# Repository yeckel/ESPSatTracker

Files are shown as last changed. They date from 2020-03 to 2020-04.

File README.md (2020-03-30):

# ESPSatTracker (work still in progress, ideas wellcommend)

This project is intended for tracking HAM radio satellites using stock available cheep components and 3D printer. 
* Antena is 5+8 elem Yagi from [dk7zb](https://www.qsl.net/dk7zb/Duoband/5+8_2m-70cm.htm)
* Rotator was heavily inspired from [tysonpower.de](https://tysonpower.de/blog/diy-az-el-antenna-rotator-for-under-150)

## Features
It shall be remotely operated (Bluetooth), it shall bear heavier antennas (preparing for moonscating), it shall be portable, it shall bring fun.

## Parts used
* 2000 x 15 x 15 allu rectangle tube for antenna beam
* two 2000 x 20 x 20 allu rectangle tube for rotator frame and azimuth axe
* ?x 8mm allu tubes for yagi elements
* 1x 12mm allu tube for yagi radiator
* plenty of M4 screws with nuts and waschers
* 4mm plywood for rotator sides
* 2x TB6600 stepper drivers
* 2x NEMA24 stepper motors
* 2 endstops from eBay (optional and not really used)
* Wemos Lolin32 as rotator controller (other ESP32 development board should do too)
* PLA filanment (ABS was bending too much for big parts)

## Software used
* OpenSCAD & Slic3r & RepetierHost for 3d modelling and printing
* [platformio](https://platformio.org) for SW build
* gpredict for satellite tracking
* STL and scad projects and fotos are at [thingiverse](https://www.thingiverse.com/thing:4246844)

## Build
### Dependencies
Install platformio and libraries Streaming and ESP8266_SSD1306
```
platformio lib --global install Streaming
platformio lib --global install ESP8266_SSD1306
```
### Build and upload:
Run in the RotatorController directory
```
platformio run -t upload
```

### Start
1. Without power, orient the rotator to the north and level antena horizontally.
1. Power up motors and ESP32 controller
1. In your bluetooth search for a device named ESP32 Rotator and add that device.
1. In the terminal connect to it `sudo rfcomm connect 1 <device mac address>`
1. In another terminal window start a rotator control daemon `rotctld -r /dev/rfcomm1 -s 115200 -m 603` The 603 is a rotator model 603, 'GS-232B'
1. Then in gpredict add a new rotator. Choose some name, host is `localhost`, port: `4533`, Az type: `0 - 180 - 360`, Max Az:`360`, Max El: `180`

## Notes
The rotator can commands like speed and park to zero. However the rotctld nor it's stand-allone application are using them. Just stop, move to azimuth and elevation, asking for current azimuth and elevation is actually used by the daemon.

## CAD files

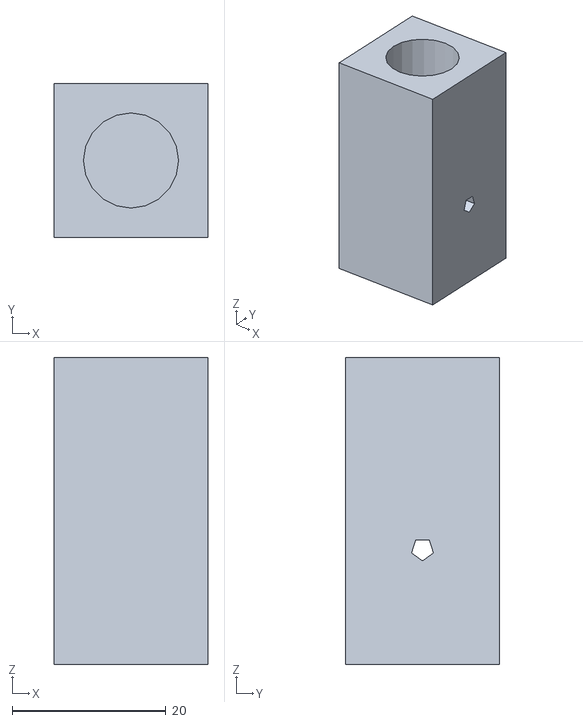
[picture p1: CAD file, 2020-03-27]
3dPrintedParts/stls/RadiatorDrillTool.stl
20.0 x 20.0 x 40.0

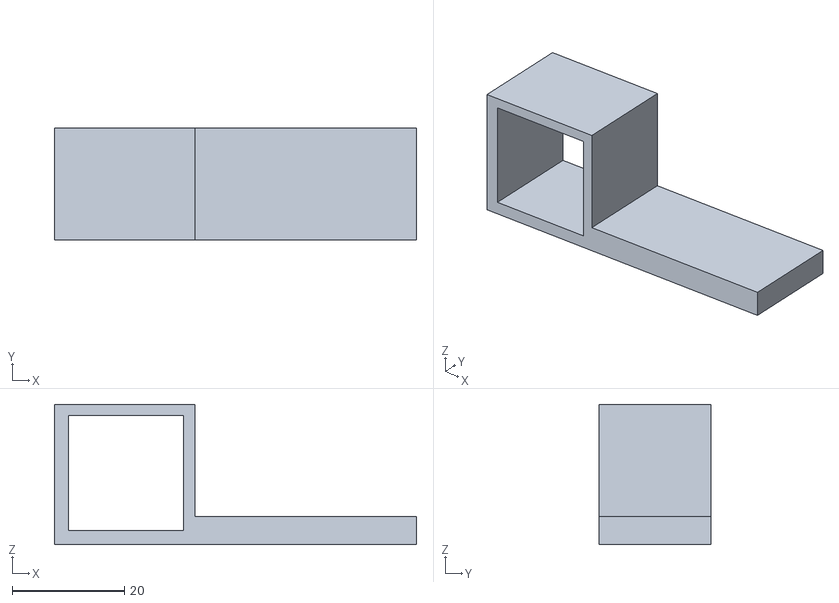
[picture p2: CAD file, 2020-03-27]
3dPrintedParts/stls/endstopEle.stl
64.5 x 20.0 x 25.0

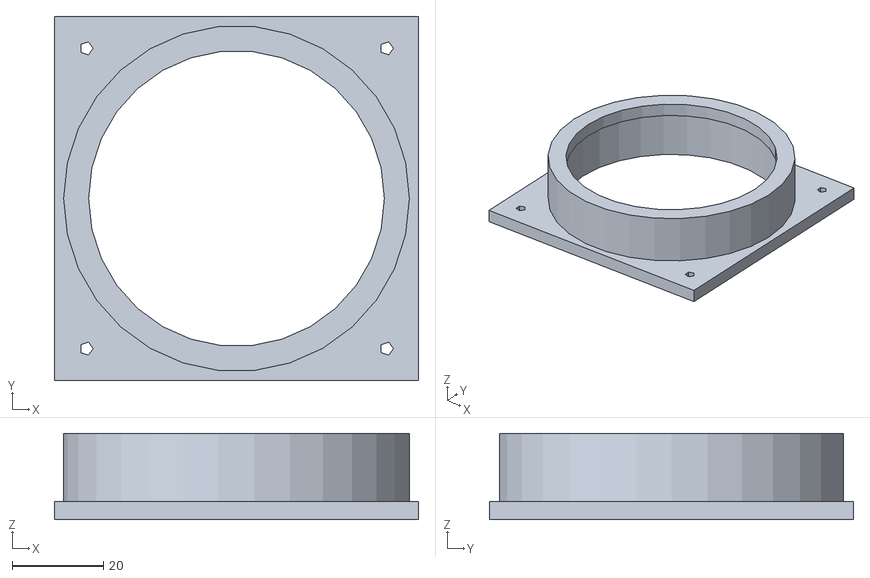
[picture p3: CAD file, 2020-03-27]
3dPrintedParts/stls/bearingHolder.stl
80.0 x 80.0 x 19.0

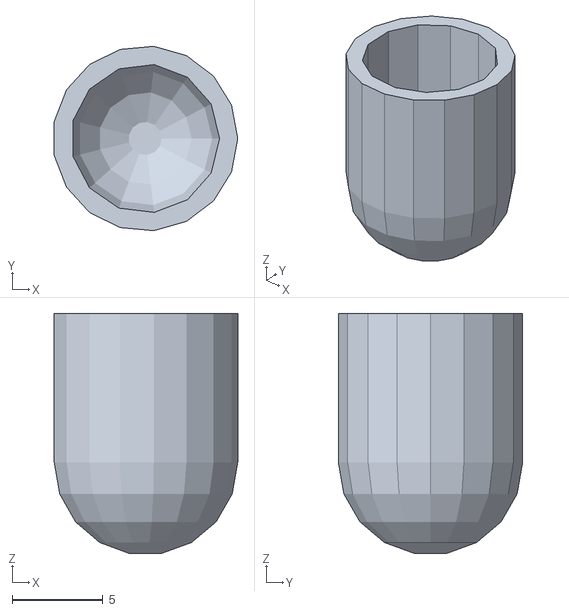
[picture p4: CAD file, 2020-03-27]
3dPrintedParts/stls/WireCap.stl
10.1 x 10.2 x 13.2

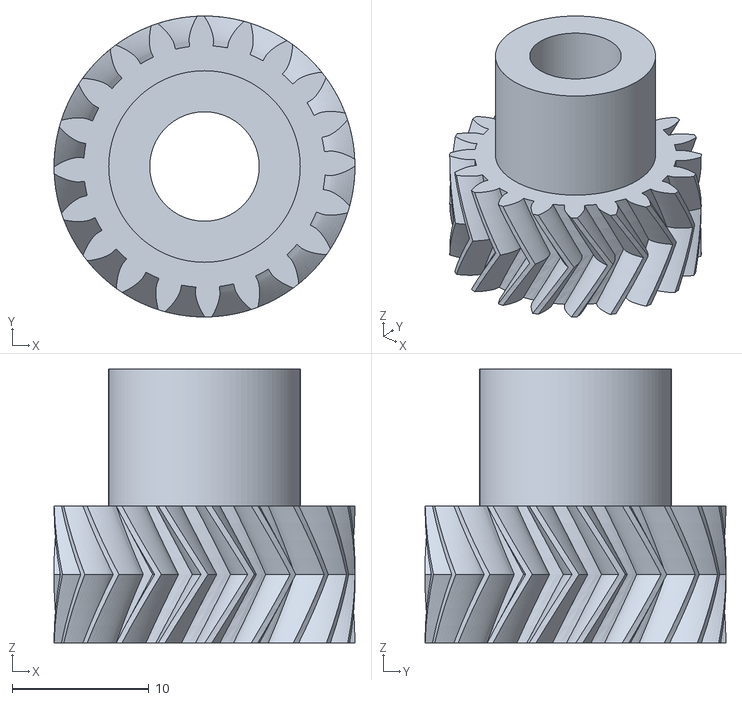
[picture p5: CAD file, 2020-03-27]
3dPrintedParts/stls/KoleckoKMotoru.stl
22.0 x 22.0 x 20.0

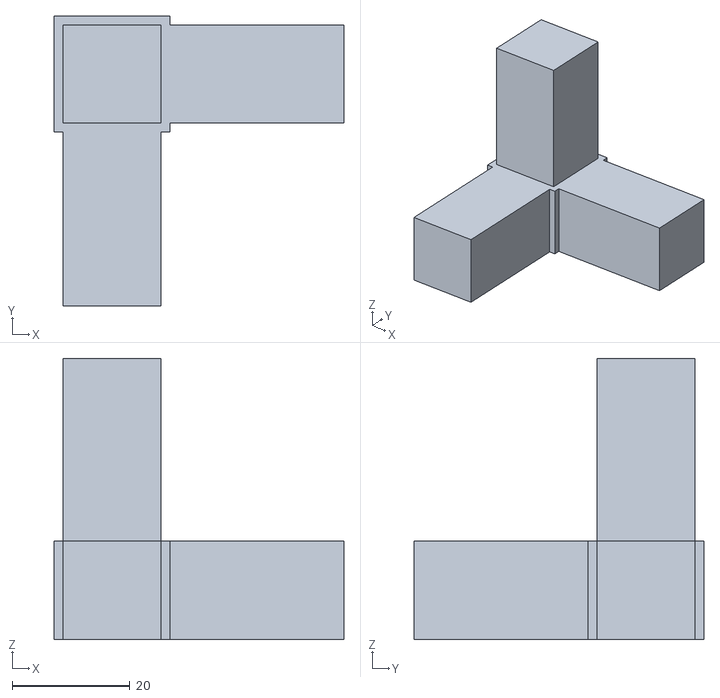
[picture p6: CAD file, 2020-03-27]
3dPrintedParts/stls/BoxCorner.stl
49.4 x 49.4 x 47.9

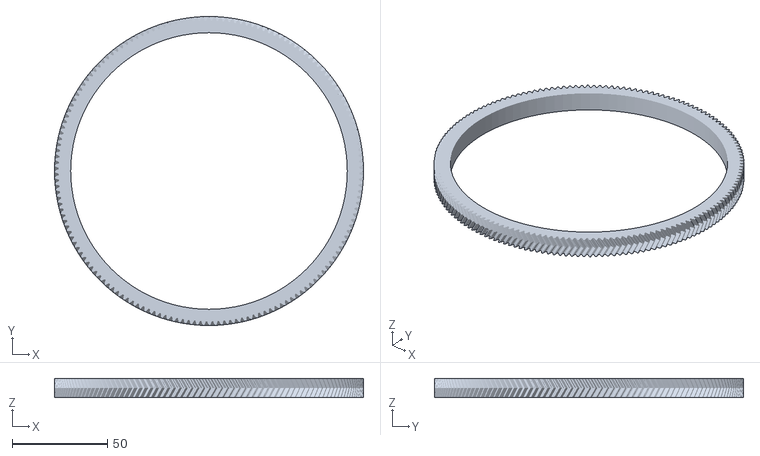
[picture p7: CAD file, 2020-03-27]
3dPrintedParts/stls/PrevodovkaRotator.stl
162.0 x 162.0 x 10.0

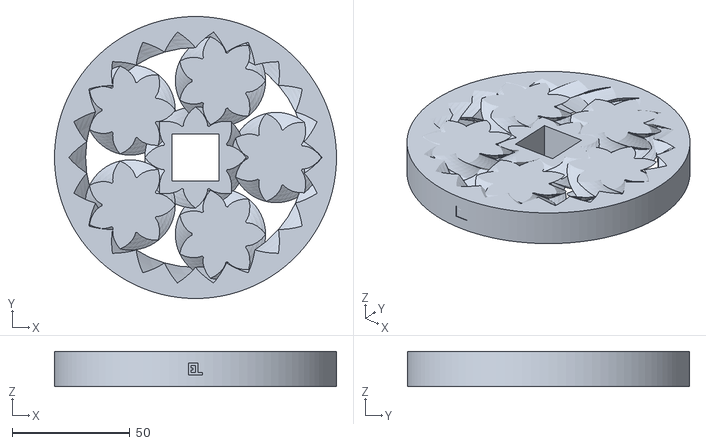
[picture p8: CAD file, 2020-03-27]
3dPrintedParts/stls/bearing.stl
120.0 x 120.0 x 15.0

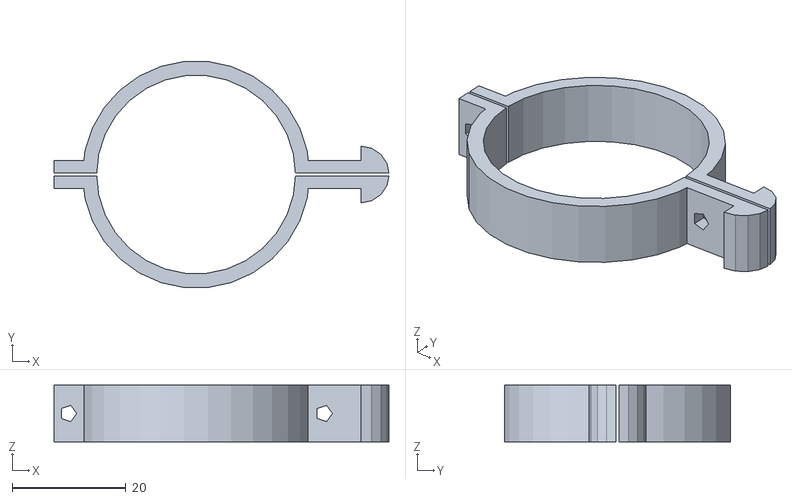
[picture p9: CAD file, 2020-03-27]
3dPrintedParts/stls/endstopAzi.stl
59.0 x 39.8 x 10.0

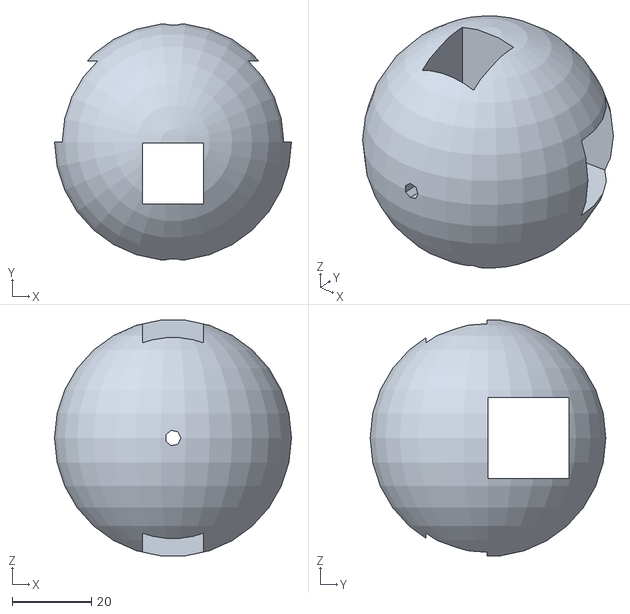
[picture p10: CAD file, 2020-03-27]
3dPrintedParts/stls/mast2yagi.stl
60.0 x 59.7 x 59.7

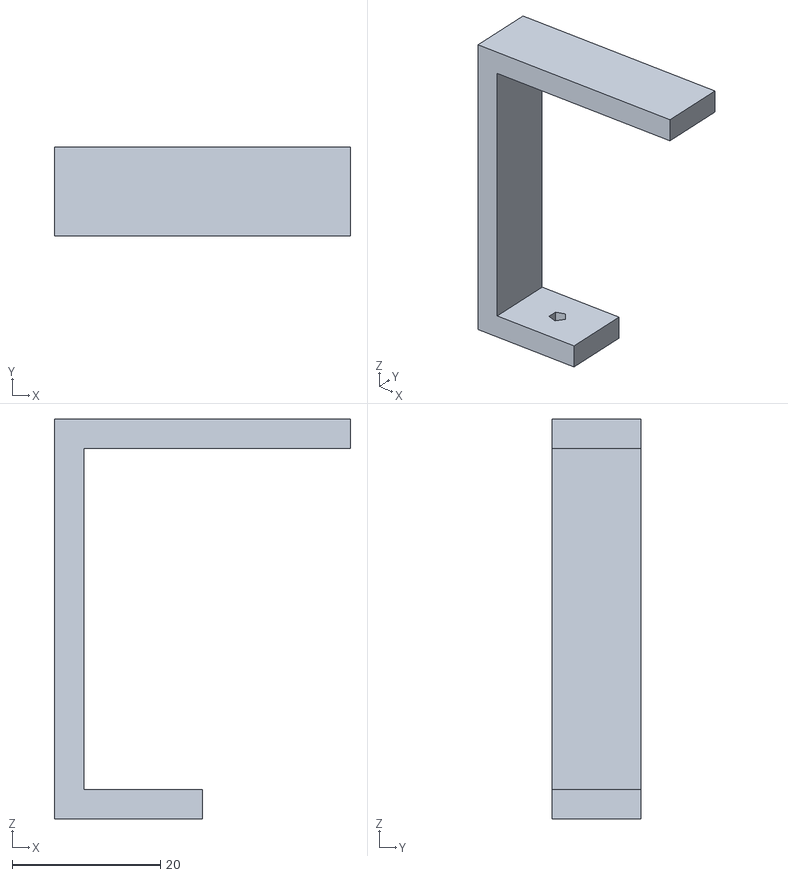
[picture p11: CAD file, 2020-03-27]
3dPrintedParts/stls/endstopHolder.stl
40.0 x 12.0 x 54.0

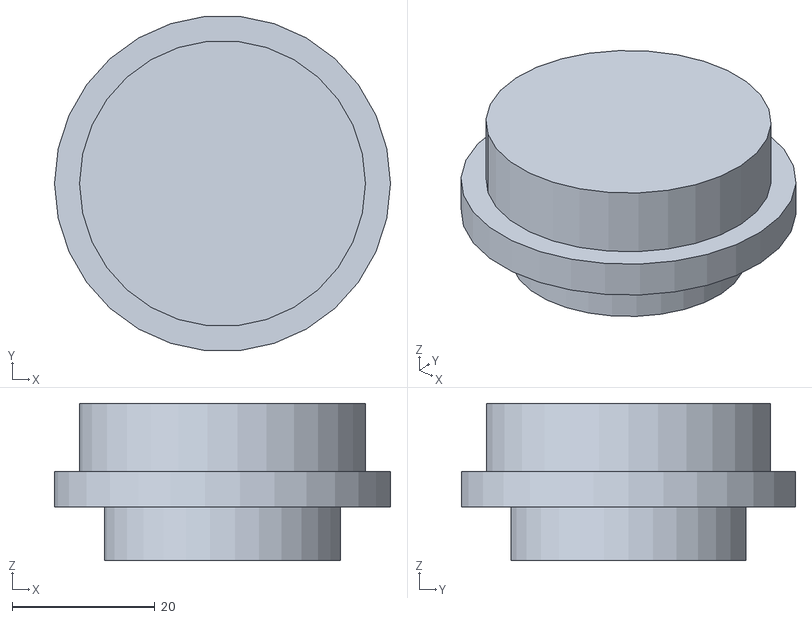
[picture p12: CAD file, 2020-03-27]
3dPrintedParts/stls/tripodCap.stl
47.0 x 46.7 x 22.0

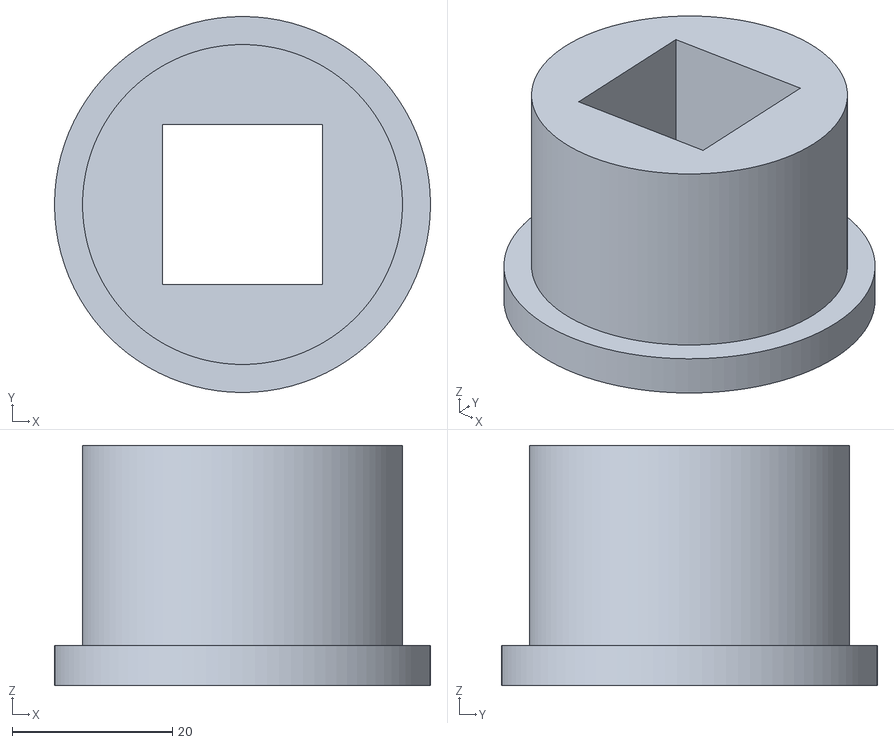
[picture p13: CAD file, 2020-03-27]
3dPrintedParts/stls/elevationHolder.stl
47.0 x 47.0 x 30.0

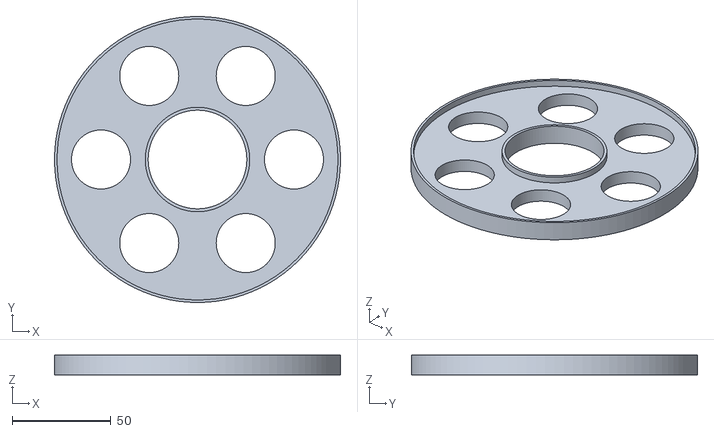
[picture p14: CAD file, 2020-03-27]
3dPrintedParts/stls/gearCenter.stl
145.0 x 145.0 x 10.0

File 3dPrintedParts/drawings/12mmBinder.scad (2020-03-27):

cylinder(h=50,d=10,center=true);
cylinder(h=2,d=12,center=true);

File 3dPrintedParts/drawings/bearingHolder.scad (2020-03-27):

difference(){
union(){
cylinder(d=76,h=19);//obal loziska stena 4mm
translate([0,0,2]) cube([80,80,4],center=true); //podstavec
}
cylinder(d=69,h=15); //lozisko
cylinder(d=65,h=30); //vnitrek loziska

translate([33,33,0]) cylinder(d=3,h=20);
translate([-33,-33,0]) cylinder(d=3,h=20);
translate([33,-33,0]) cylinder(d=3,h=20);
translate([-33,33,0]) cylinder(d=3,h=20);
}

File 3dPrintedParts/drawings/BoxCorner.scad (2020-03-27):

profil=20/1.013;
stena=3*1.4;

vnitek=profil-stena;

rotate([0,0,0]) translate([0,0,profil])cube([vnitek,vnitek,2*profil],center = true);
rotate([0,90,0]) translate([0,0,profil])cube([vnitek,vnitek,2*profil],center = true);
rotate([90,0,0]) translate([0,0,profil])cube([vnitek,vnitek,2*profil],center = true);
cube([profil,profil,profil-stena], center = true);

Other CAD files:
3dPrintedParts/stls/OuterGearRing.stl
3dPrintedParts/stls/yagi_director.stl
3dPrintedParts/stls/azimuthCoreWheel.stl
3dPrintedParts/stls/elevationCoreWheel.stl
3dPrintedParts/drawings/endstopAzi.scad
3dPrintedParts/drawings/RadiatorDrillTool.scad
3dPrintedParts/drawings/Rotator.scad
3dPrintedParts/drawings/Spojka90Stupnu.scad
3dPrintedParts/drawings/WireCap.scad
3dPrintedParts/drawings/endstopEle.scad
3dPrintedParts/drawings/endstopHolder.scad
3dPrintedParts/drawings/mast2yagi.scad
3dPrintedParts/drawings/tripodCap.scad
3dPrintedParts/drawings/yagi_director.scad
3dPrintedParts/drawings/yagi_radiator.scad

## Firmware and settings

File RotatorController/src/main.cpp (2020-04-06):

#include <Arduino.h>
#include <SSD1306Wire.h>
#include "BluetoothSerial.h"
#include <Streaming.h>

// DIY Sat Tracker Software by Tysonpower.de
// NOTE: The code works but it is NOT optimal nor bug free

// Implementation of the Yaesu GS232B Protocol
// B              - Report elevation                                EL=eee
// C              - Report azimuth                                  AZ=aaa
// C2             - Report azimuth and elevation                    AZ=888 EL=eee
// S              - Stop all rotation
// A              - Stop azimuth rotation
// E              - Stop elevation rotation
// L              - Rotate azimuth left (CCW)
// R              - Rotate azimuth right (CW)
// D              - Rotate elevation down
// U              - Rotate elevation up
// Mxxx           - Move to azimuth
// Wxxx yyy       - Move to azimuth xxxx and elevation yyy
// X1             - Change to azimuth rotation speed setting 1
// X2             - Change to azimuth rotation speed setting 2
// X3             - Change to azimuth rotation speed setting 3
// X4             - Change to azimuth rotation speed setting 4
// O              - Azimuth offset calibration
// F              - Azimuth full scale calibration
// O2             - Elevation offset calibration
// F2             - Elevation full scale calibration
// P36            - Switch to 360 degree mode
// P45            - Switch to 450 degree mode
// Z              - Toggle north / south centered mode
// H              - Help

#define EL_ENDSTOP 25
#define AZ_ENDSTOP 26

#define AZ_ENABLE 16
#define EL_ENABLE 2
// Pins Stepper EL
#define EL_PUL 13
#define EL_DIR 12
// Pins Stepper AZ
#define AZ_PUL 15
#define AZ_DIR 14

void drawDisplay();
void serialEventBT();
void handleSerialCommand(String);
int getElevation();
int getAzimuth();
void setElevation(int elevation);
void setAzimuth(int azimuth);

void setStepFrequency(int frequencyHz);

// Function to stop the EL axis
void stopElevationMoving();

// Function to stop the AZ axis
void stopAzimuthMoving();

// Function to zero out the EL axis
void findElevationZero();

// Function to zero out the AZ axis
void findAzimuthZero();

// FUll calibration to get STepps per 360°
// Function to calibrate the trackers EL axis
void calibrateStepsOnElevation();

// Function to calibrate the trackers AZ axis
void calibrateAzimuthSteps();

void azInterrupt();
void elInterrupt();

int getAzDirection();
int getElDirection();

void moveToElevation();
void moveToAzimuth();

void moveStepperOneDeg(int PULpin, int DIRpin, bool rev);
void moveStepperOneStep(int PULpin, int DIRpin, bool rev);
//////////////////////Variables//////////////////////////
volatile int m_azDirection{0};
volatile int m_elDirection{0};
volatile unsigned m_azimuthSteps{0}, m_elevationSteps{0};

static constexpr unsigned STEPS_PER_REVOLUTION{51250};
static constexpr unsigned STEPS_PER_DEGREE{51250 / 360}; //142

static constexpr unsigned PWM_RESOUTION{8};
static constexpr unsigned PWM_DUTY_CYCLE_ON{255 / 4};
static constexpr unsigned PWM_DUTY_CYCLE_OFF{0};
static constexpr unsigned CHANNEL_EL{0};
static constexpr unsigned CHANNEL_AZ{1};

volatile bool justCalibratedAz{false};
volatile bool justCalibratedEl{false};

unsigned m_step_frequency{2500};
unsigned m_desiredAzimuthSteps{0}, m_desiredElevationSteps{0};

SSD1306Wire display(0x3c, 5, 4, GEOMETRY_128_64);
BluetoothSerial ESP_BT;

String sdata = "";
bool processCommandFlag{false};

void setup()
{
    ESP_BT.begin("ESP32 Rotator");
    Serial.begin(115200);

    ESP_BT.println("Sat rotator!");

    display.init();
    display.flipScreenVertically();
    display.setTextAlignment(TEXT_ALIGN_LEFT);

    pinMode(AZ_ENABLE, OUTPUT);
    pinMode(EL_ENABLE, OUTPUT);

    pinMode(EL_DIR, OUTPUT);
    pinMode(AZ_DIR, OUTPUT);

    pinMode(EL_ENDSTOP, INPUT);
    pinMode(AZ_ENDSTOP, INPUT);

    ledcSetup(CHANNEL_EL, m_step_frequency, PWM_RESOUTION);
    ledcSetup(CHANNEL_AZ, m_step_frequency, PWM_RESOUTION);

    ledcAttachPin(EL_PUL, CHANNEL_EL);
    ledcAttachPin(AZ_PUL, CHANNEL_AZ);

    attachInterrupt(EL_PUL, elInterrupt, RISING);
    attachInterrupt(AZ_PUL, azInterrupt, RISING);
}

void loop()
{
    drawDisplay();

    if(ESP_BT.available())
    {
        serialEventBT();
    }

    if(processCommandFlag)
    {
        processCommandFlag = false;
        handleSerialCommand(sdata);
        sdata = "";
    }
}

void drawDisplay()
{
    display.clear();
    display.setFont(ArialMT_Plain_24);
    display.drawString(0, 0, "AZ=" + String(getAzimuth()));
    display.drawString(0, 22, "EL=" + String(getElevation()));
    if(ESP_BT.hasClient())
    {
        display.drawString(100, 0, "C");
    }
    else
    {
        display.drawString(100, 0, "N");
    }
    display.setFont(ArialMT_Plain_16);
    display.drawString(0, 48, "E" + String(digitalRead(EL_ENDSTOP)) +
                       "A" + String(digitalRead(AZ_ENDSTOP)) +
                       " E" + String(getElDirection()) +
                       " A" + String(getAzDirection())) ;
    display.display();
}

void handleSerialCommand(String serialIn)
{
    Serial.println("Command:" + serialIn);
    if(serialIn.startsWith("C2"))
    {
        Serial.println("Report az and el");
        ESP_BT.print("AZ=" + String(getAzimuth()) + " EL=" + String(getElevation()));
        ESP_BT.print("\r\n");
        return;
    }
    if(serialIn.startsWith("S"))
    {
        Serial.println("Stop all rotation");
        ESP_BT.print("\r\n");
        stopElevationMoving();
        stopAzimuthMoving();
        justCalibratedAz = false;
        justCalibratedEl = false;
        return;
    }
    if(serialIn == "B")                                   // Report elevation (el)
    {
        ESP_BT.print("EL=" + String(getElevation()));
        ESP_BT.print("\r\n");
    }
    else if(serialIn == "C")                              // Report azimuth (az)
    {
        ESP_BT.print("AZ=" + String(getAzimuth()));
        ESP_BT.print("\r\n");
    }
    if(serialIn == "A")                            // Stop az rotation
    {
        stopAzimuthMoving();
    }
    else if(serialIn == "E")                              // Stop el rotation
    {
        stopElevationMoving();
    }
    else if(serialIn == "L")                              // rotate azimuth left (CCW)
    {

    }
    else if(serialIn == "R")                              // rotate azimuth right (CW)
    {

    }
    else if(serialIn == "D")                              // rotate elevation down
    {

    }
    else if(serialIn == "U")                              // rotate elevation up
    {

    }
    else if(serialIn.substring(0, 1) == "M")              // Move to azimuth
    {
        ESP_BT.print("\r\n");
        setAzimuth(serialIn.substring(1, 4).toInt());
    }
    else if(serialIn.substring(0, 1) == "W")              // Move to azimuth and elevation
    {
        ESP_BT.print("\r\n");
        setAzimuth(serialIn.substring(1, 4).toInt());
        setElevation(serialIn.substring(5, 8).toInt());
    }
    else if(serialIn == "X1")                             // Azimuth rotation speed 1
    {
        setStepFrequency(7000);
    }
    else if(serialIn == "X2")                             // Azimuth rotation speed 2
    {
        setStepFrequency(5000);
    }
    else if(serialIn == "X3")                             // Azimuth rotation speed 3
    {
        setStepFrequency(3500);
    }
    else if(serialIn == "X4")                             // Azimuth rotation speed 4
    {
        setStepFrequency(2500);
    }
    else if(serialIn == "O")                              // Azimuth offset calibration
    {
        findAzimuthZero();
    }
    else if(serialIn == "F")                              // Azimuth full scale calibration
    {

    }
    else if(serialIn == "O2")                             // Elevation offset calibration
    {
        findElevationZero();
    }
    else if(serialIn == "F2")                             // Elevation full scale calibration
    {
        calibrateStepsOnElevation();
    }
    else if(serialIn == "P36")                            // Switch to 360 degree mode
    {

    }
    else if(serialIn == "P45")                            // Switch to 450 degree mode
    {

    }
    else if(serialIn == "Z")                              // Toggle north/South centered mode
    {

    }
    else if(serialIn == "H")                              // Help
    {

    }
}

void serialEventBT()
{
    while(ESP_BT.available())
    {
        auto inChar = (char)ESP_BT.read();
        //Serial.println(inChar, HEX);
        sdata += inChar;

        if(inChar == 0x0D)
        {
            sdata.trim();
            processCommandFlag = true;
        }
    }
}

void azInterrupt()
{
    m_azimuthSteps += m_azDirection;
    if(m_azimuthSteps == m_desiredAzimuthSteps)
    {
        justCalibratedAz = false;
        m_azDirection = 0;
        ledcWrite(CHANNEL_AZ, PWM_DUTY_CYCLE_OFF);
    }
}

void elInterrupt()
{
    //Serial << __FUNCTION__ << m_elevationSteps << " " << m_elDirection << endl;
    m_elevationSteps += m_elDirection;
    if(m_elevationSteps == m_desiredElevationSteps)
    {
        justCalibratedEl = false;
        m_elDirection = 0;
        ledcWrite(CHANNEL_EL, PWM_DUTY_CYCLE_OFF);
    }
}

int getAzDirection()
{
    return m_azDirection;
}

int getElDirection()
{
    return m_elDirection;
}

int getElevation()
{
    return (m_elevationSteps + 1) / STEPS_PER_DEGREE;
}
int getAzimuth()
{
    return (m_azimuthSteps + 1) / STEPS_PER_DEGREE;
}

void setElevation(int elevation)
{
    if(elevation > 180)
    {
        return;
    }
    m_desiredElevationSteps = elevation * STEPS_PER_DEGREE;
    moveToElevation();
}

void setAzimuth(int azimuth)
{
    if(azimuth > 450)
    {
        return;
    }
    m_desiredAzimuthSteps = azimuth * STEPS_PER_DEGREE;
    moveToAzimuth();
}

void startELdown()
{
    digitalWrite(EL_DIR, HIGH);
    ledcWrite(CHANNEL_EL, PWM_DUTY_CYCLE_ON);
}

void startELUp()
{
    digitalWrite(EL_DIR, LOW);
    ledcWrite(CHANNEL_EL, PWM_DUTY_CYCLE_ON);
}

void moveToElevation()
{
    Serial << __FUNCTION__ << " desired:" << m_desiredElevationSteps << " is:" << m_elevationSteps << endl;
    if(m_desiredElevationSteps < m_elevationSteps)
    {
        startELdown();
        m_elDirection = -1;
    }
    else if(m_desiredElevationSteps > m_elevationSteps)
    {
        startELUp();
        m_elDirection = +1;
    }
}

void startAzRight()
{
    ledcWrite(CHANNEL_AZ, PWM_DUTY_CYCLE_ON);
    digitalWrite(AZ_DIR, LOW);
}

void startAzLeft()
{
    ledcWrite(CHANNEL_AZ, PWM_DUTY_CYCLE_ON);
    digitalWrite(AZ_DIR, HIGH);
}

void moveToAzimuth()
{
    Serial << __FUNCTION__ << " desired:" << m_desiredAzimuthSteps << " is:" << m_azimuthSteps << endl;
    if(m_desiredAzimuthSteps < m_azimuthSteps)
    {
        startAzLeft();
        m_azDirection = -1;
    }
    else if(m_desiredAzimuthSteps > m_azimuthSteps)
    {
        startAzRight();
        m_azDirection = +1;
    }
}

void stopElevationMoving()
{
    Serial << __FUNCTION__ << endl;
    m_elDirection = 0;
    ledcWrite(CHANNEL_EL, PWM_DUTY_CYCLE_OFF);
}

// Function to stop the AZ axis
void stopAzimuthMoving()
{
    Serial << __FUNCTION__ << endl;
    m_azDirection = 0;
    ledcWrite(CHANNEL_AZ, PWM_DUTY_CYCLE_OFF);
}

// Function to zero out the EL axis
void findElevationZero()
{
    Serial << __FUNCTION__ << endl;
}

// Function to zero out the AZ axis
void findAzimuthZero()
{
    Serial << __FUNCTION__ << endl;
}

//Shall run between two endstops, but i have just one on 0
void calibrateStepsOnElevation()
{
    Serial << __FUNCTION__ << endl;
    //calibrate steps
}

//Shall run one complete round and calculate steps
void calibrateAzimuthSteps()
{
    Serial << __FUNCTION__ << endl;
    //calibrate steps
}

void setStepFrequency(int frequencyHz)
{
    m_step_frequency = frequencyHz;
    ledcWriteTone(CHANNEL_EL, m_step_frequency);
    ledcWriteTone(CHANNEL_AZ, m_step_frequency);
}

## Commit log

2020-03-29 Implemented endstops and endstop calibration
2020-03-29 Debouncing endstops
2020-04-06 Removed end stops handling, extended range to 450, 180
    It was causing issues during turning. PRobably some glitches were
    resetting coordinates and the rotator was turning around over 360
    degree.
    [main.cpp]
